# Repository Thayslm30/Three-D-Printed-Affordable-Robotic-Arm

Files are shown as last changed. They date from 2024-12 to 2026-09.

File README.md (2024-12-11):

# T.A.R.A. - Three-D Printed Affordable Robotic Arm

This repository includes the code, 3D printing files, and documentation to build the industrial robot arm named **T.A.R.A.**. This project aims to make robotics accessible by providing a low-cost and customizable solution for education, research, and small-scale industry applications.



---

## What's Included

This repository contains:

1. **3D Printing Files**: STL files for all robot parts.
2. **Electronics and Circuit Diagrams**: Wiring guides.
3. **Software**:
   - Arduino code to control de robot
   - Arduino code for troubleshooting
   - Jupyter Notebobks with the Python code to run simulations of the robot
4. **Documentation**:
   - Bill of materials (BOM) https://docs.google.com/document/d/1PwCRcLvzc4oVpurYSVTbRW2TU2EedRhl2yPV-Ze2hmc/edit?usp=sharing

---

## Getting Started

### Prerequisites

To replicate this project, you’ll need the following:
- **3D Printer**: Compatible with PLA or ABS filament.
- **Electronics**: 
  - Microcontroller (Arduino)
  - Servo motors (MG996R, SG90SR, etc.)
  - Power supply and wires
- **Software**:
  - Python 3.8+ https://www.python.org
  - Arduino IDE (for firmware upload) https://www.arduino.cc/en/software
  - Autodesk Fusion 360 (or any software that allows you to view and modify the 3D printing .stl files) https://www.autodesk.com/products/fusion-360/overview?term=1-YEAR&tab=subscription
  - Jupyter Notebook https://docs.jupyter.org/en/latest/
  - Pinocchio Library https://stack-of-tasks.github.io/pinocchio/
  - Meshcat Library https://pypi.org/project/meshcat/
  - Conda for environment management https://anaconda.org/anaconda/conda

### Steps to Build

1. **Clone the Repository**:
   ```bash
   git clone https://github.com/Thayslm30/Three-D-Printed-Affordable-Robotic-Arm.git
2.  **3D Print the parts**:
     - All the parts can be printed with a 20% infill, except for the base, which has to be 50% to be able to handle the weight of all the robot.
     - All the parts can be printed without supports and without adhesions.
       
3.  **Build the circuit**:
![Figure 11](https://github.com/user-attachments/assets/9e1a0557-dbdc-4448-9370-accc07058d7d)
  
4.  **Assemble the robot**  
   - Starting from top motor at the gripper, the convention is hand servo, wrist servo, elbow servo, shoulder servo, and base servo inside the base.
   - The micro servo goes in the hand joint.
   - The standard servos are for the wrist, elbow, and base joints.
   - The High torque servo is for the shoulder joint.
   - The joints and links have spaces to pass the cables through
   - Use the complete 3D model available in the 3D printing file, to use as a reference of how the parts should fit together. Attach the halves of the links using the screws mentioned in the BOM.
   - The boards can be organized inside the base of the robot.
     
5.  **Running the code**
    - Before running the code for the first time, make sure that all the servos are physically disconnected from the links and are allowed to move freely, for them to be able to move to the zero postion for calibration.

### Demos
https://drive.google.com/drive/u/1/folders/1L06COeyFpNktWuyYnfT8AG40fpObh4bi

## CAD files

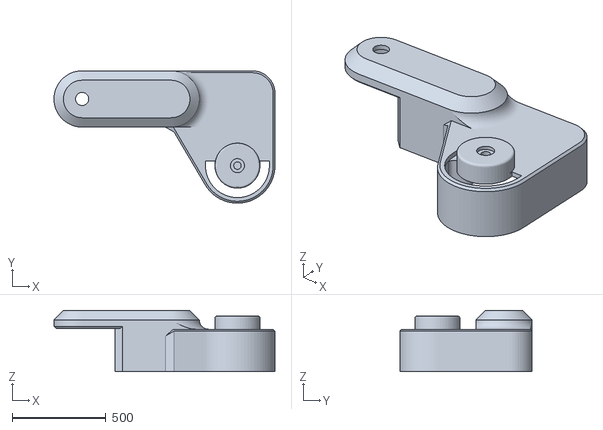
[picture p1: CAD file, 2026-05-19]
3D Printing Files/Link3a.stl
1176.8 x 705.0 x 325.0

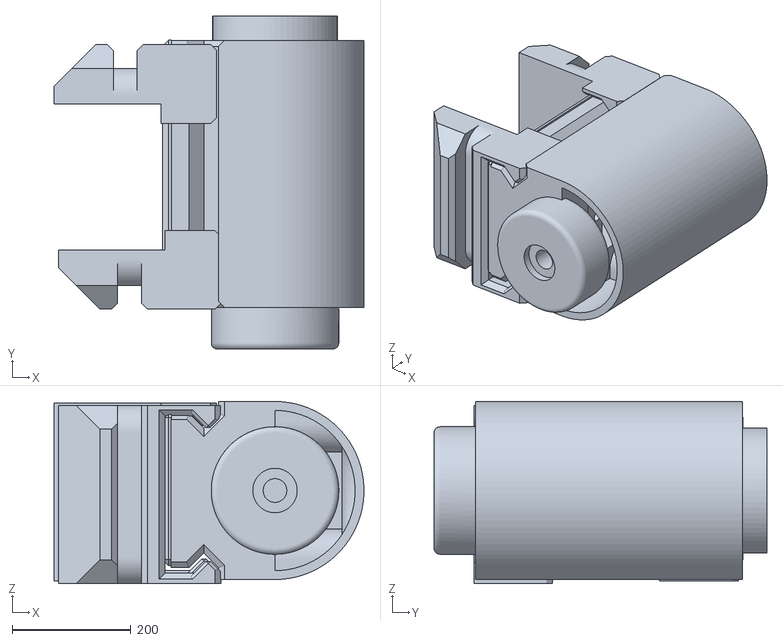
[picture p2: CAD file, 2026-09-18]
Simulation Code/EndEffector_centered.stl
522.1 x 561.0 x 306.7

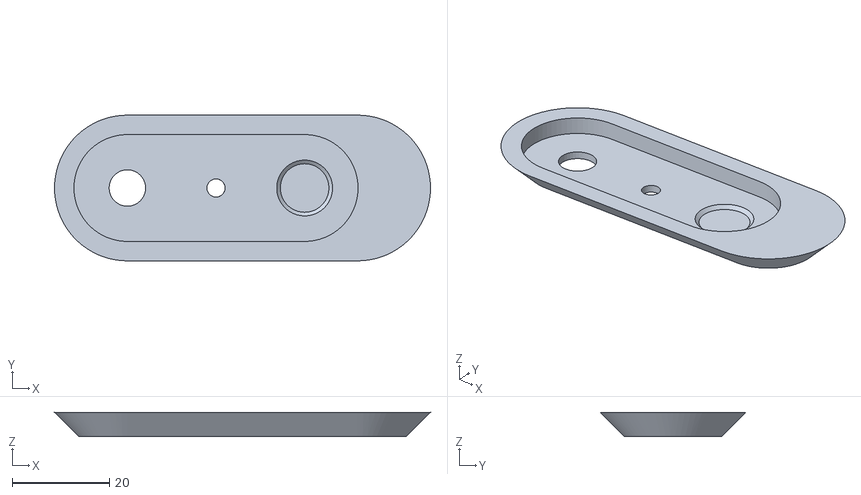
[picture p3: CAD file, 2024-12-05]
3D Printing Files/Link3c.stl
77.4 x 30.0 x 5.00

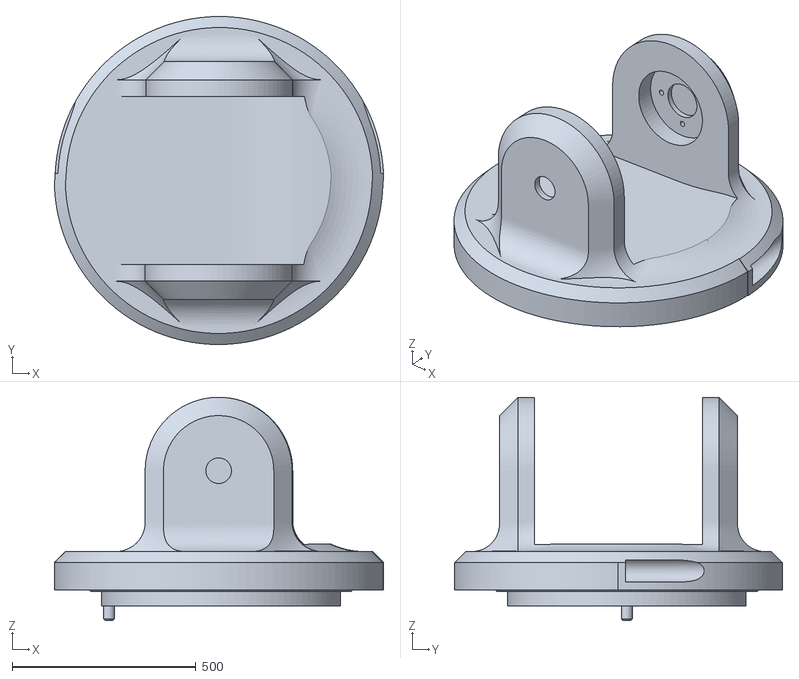
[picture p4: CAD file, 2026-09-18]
Simulation Code/Link1_centered.stl
896.9 x 893.1 x 608.3

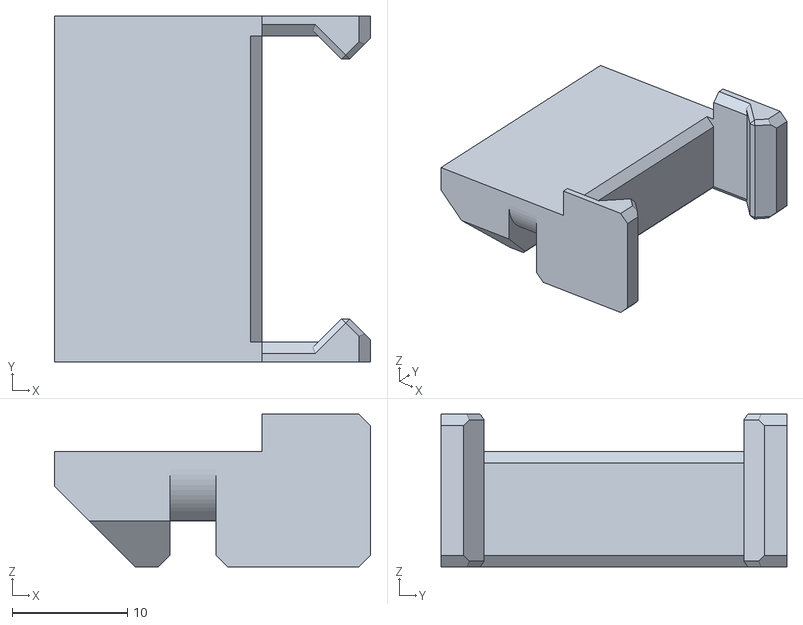
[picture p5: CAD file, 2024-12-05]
3D Printing Files/End_Effector_4.stl
27.4 x 30.0 x 13.2

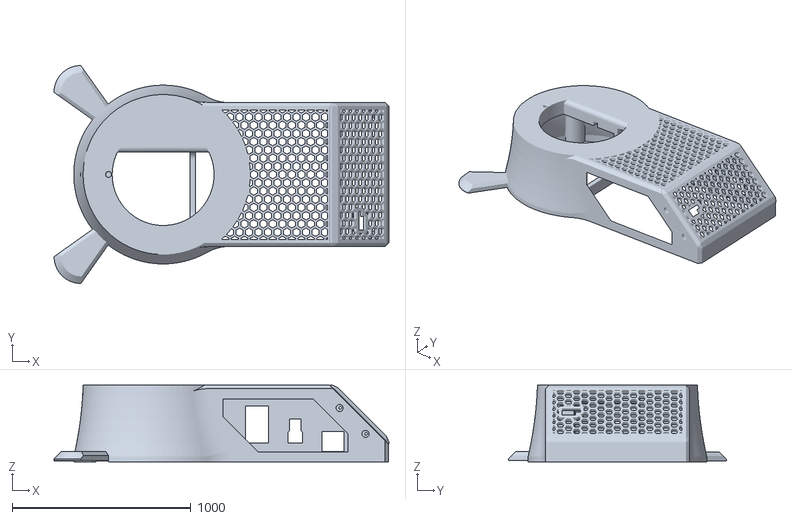
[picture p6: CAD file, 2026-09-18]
Simulation Code/Base_centered.stl
1874.0 x 1219.3 x 430.5

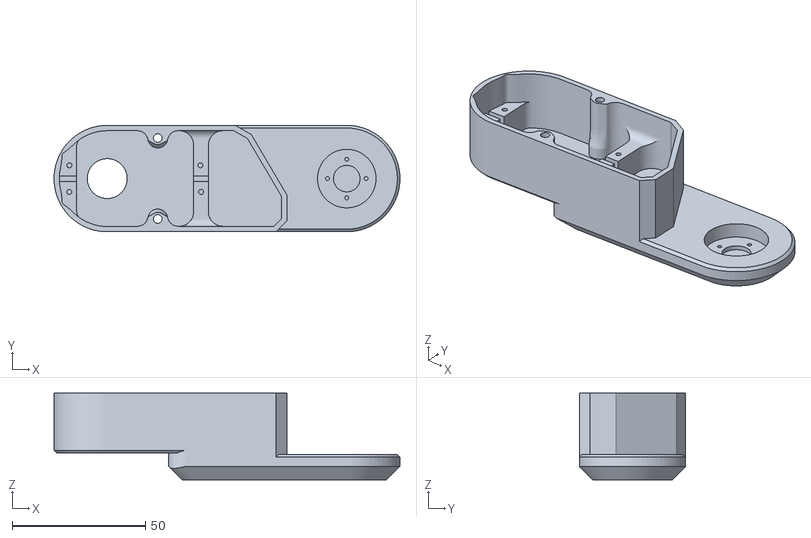
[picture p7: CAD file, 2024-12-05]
3D Printing Files/Link2b.stl
130.0 x 39.9 x 32.5

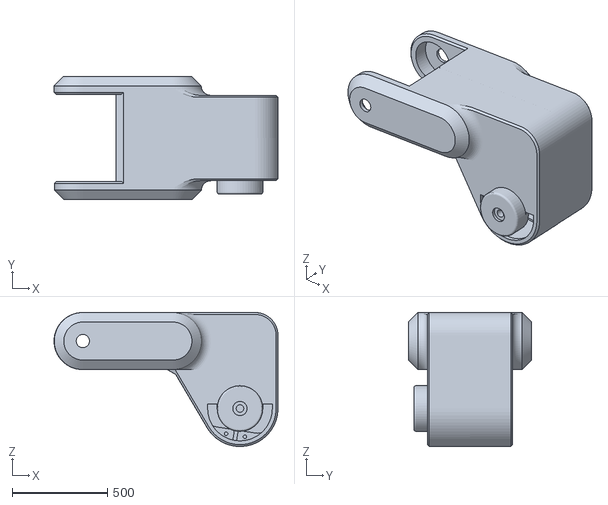
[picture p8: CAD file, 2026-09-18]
Simulation Code/Link3_centered.stl
1178.7 x 649.8 x 705.3

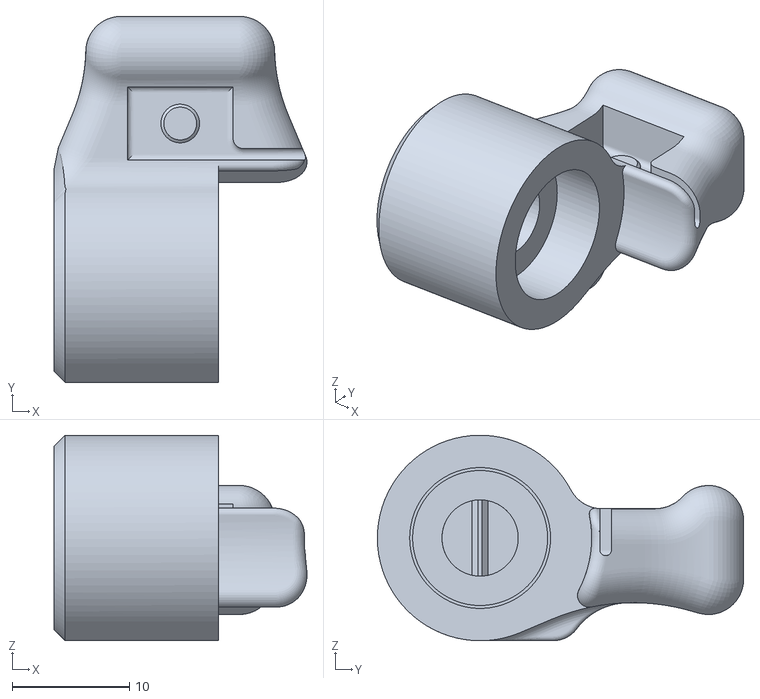
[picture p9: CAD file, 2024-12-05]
3D Printing Files/Mini_End_Effector.stl
21.5 x 31.2 x 17.5

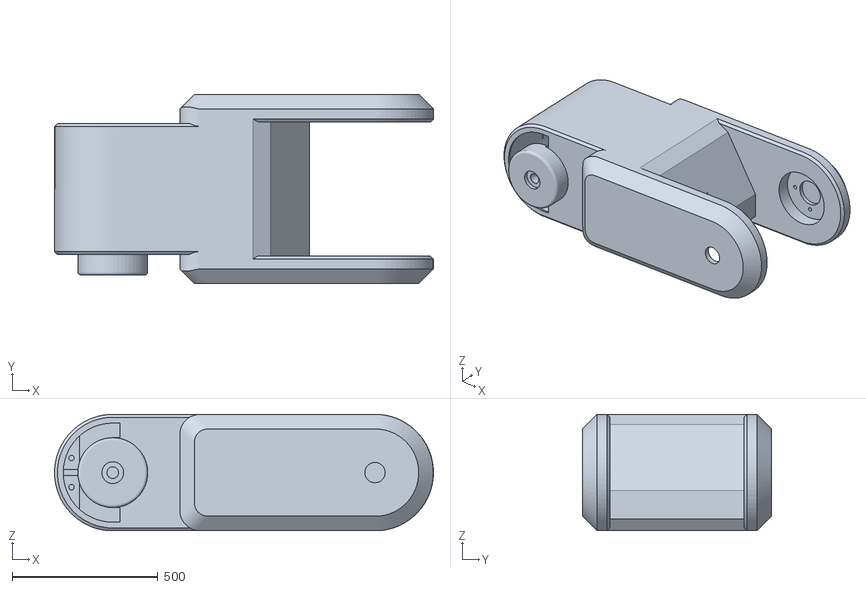
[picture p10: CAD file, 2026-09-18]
Simulation Code/Link2_centered.stl
1300.8 x 649.9 x 399.4

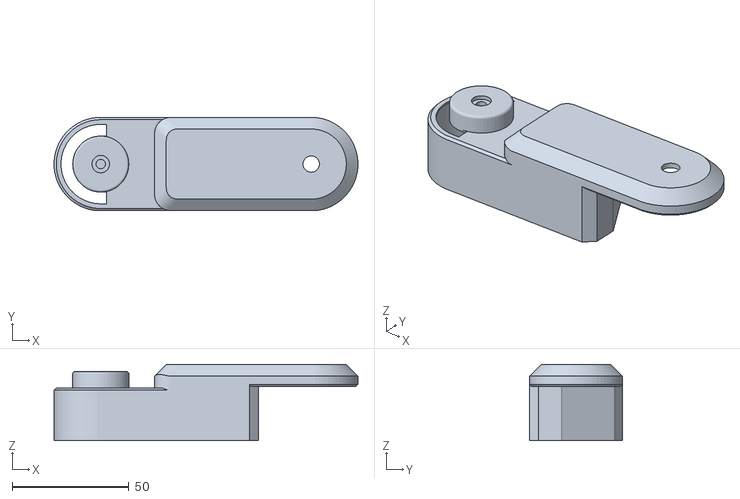
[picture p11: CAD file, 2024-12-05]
3D Printing Files/Link2a.stl
130.0 x 39.9 x 32.5

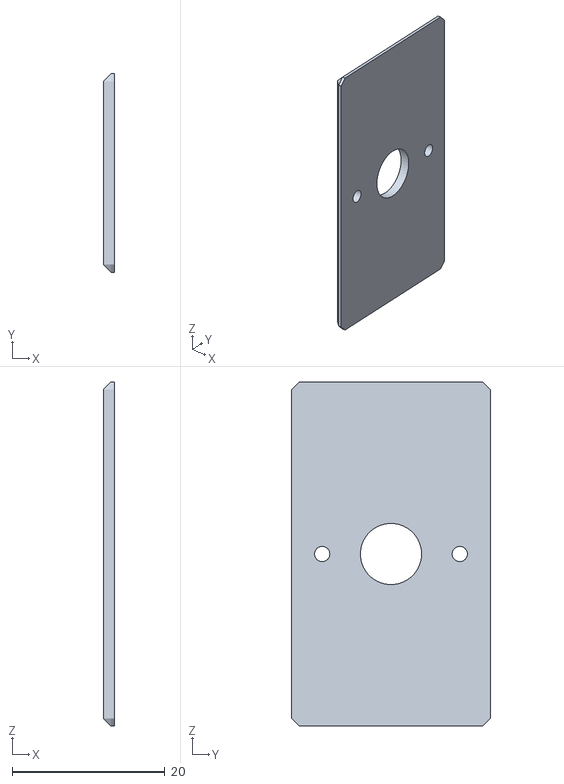
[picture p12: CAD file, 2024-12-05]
3D Printing Files/End_Effector_2.stl
1.50 x 26.0 x 45.0

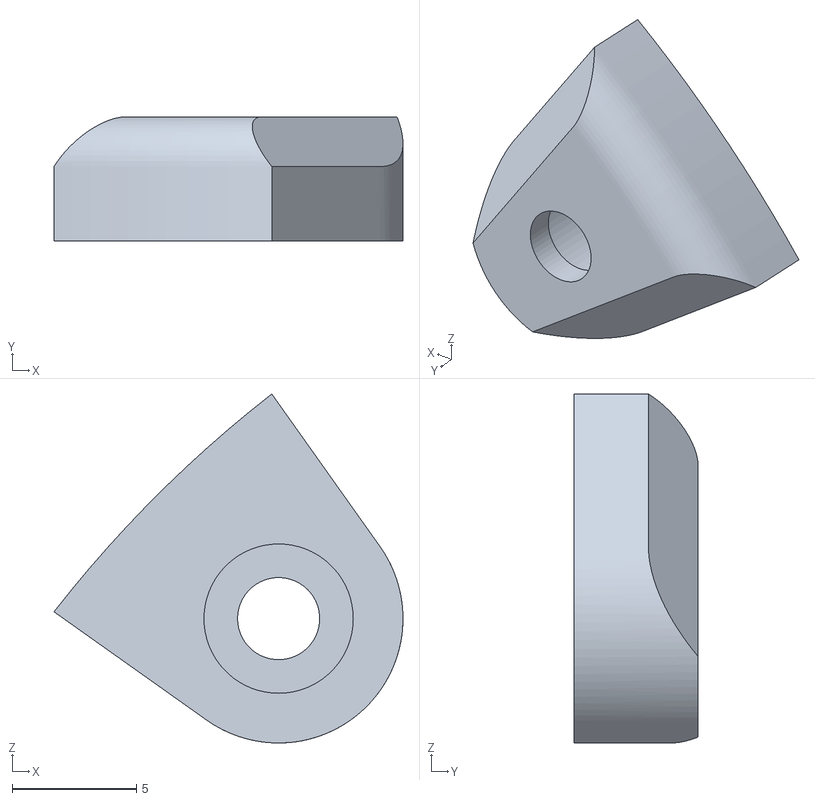
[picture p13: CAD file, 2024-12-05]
3D Printing Files/Support2.stl
14.0 x 5.00 x 14.0

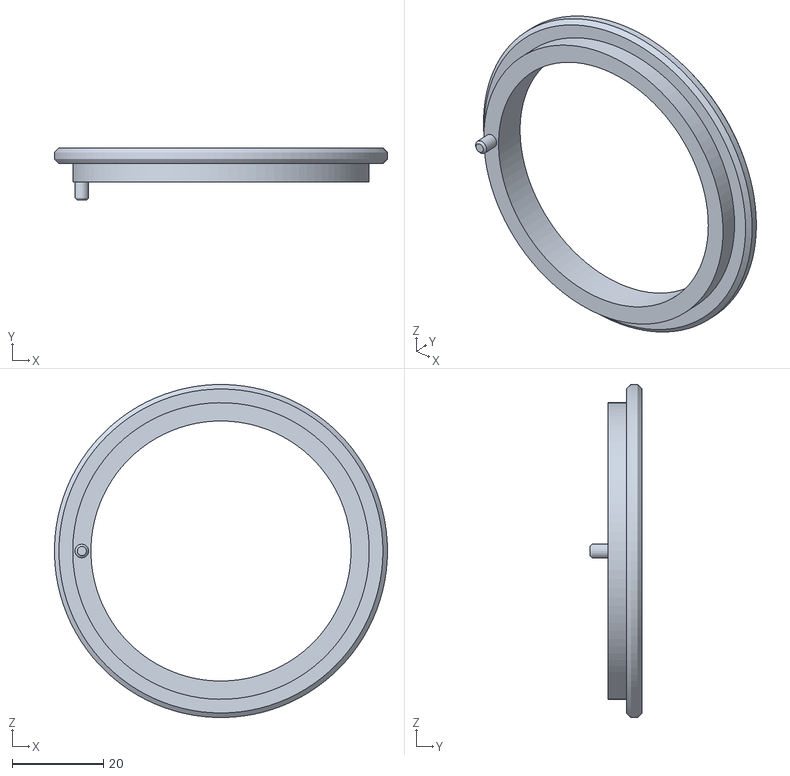
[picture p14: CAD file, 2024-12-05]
3D Printing Files/Base_ring.stl
73.0 x 11.5 x 73.0

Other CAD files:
3D Printing Files/Mini_Link3.stl
3D Printing Files/End_Effector_3.stl
3D Printing Files/Link1a.stl
3D Printing Files/Base.stl
3D Printing Files/End_Effector_1.stl
3D Printing Files/Link1b.stl
3D Printing Files/Link3b.stl
3D Printing Files/Mini_Base.stl
3D Printing Files/Mini_Link1.stl
3D Printing Files/Mini_Link2.stl

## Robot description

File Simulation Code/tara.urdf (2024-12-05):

<robot name="my_robot">
  <!-- Base link -->
  <link name="base_link">
    <visual>
      <origin xyz="0 0 0" rpy="0 0 0"/> <!-- Position the base -->
      <geometry>
        <mesh filename="Base_centered.stl" scale="0.001 0.001 0.001"/>
      </geometry>
    </visual>
  </link>

  <!-- Joint 1: Revolute joint in Z-axis -->
  <joint name="joint_1" type="revolute">
    <parent link="base_link"/>
    <child link="link_0"/>
    <!-- Place the joint where the links connect (relative to base_link) -->
    <origin xyz="0 0 0" rpy="0 0 0"/> <!-- Adjust as necessary -->
    <axis xyz="0 0 1"/> <!-- Rotation along Z-axis -->
    <limit effort="100" velocity="1.0" lower="-3.14" upper="3.14"/>
  </joint>

  <!-- Link 0 -->
  <link name="link_0">
    <visual>
      <!-- The origin should be relative to the joint, not global (relative to base_link) -->
      <origin xyz="0 0 0" rpy="0 0 0"/> <!-- Ensure this is correct -->
      <geometry>
        <mesh filename="Link1_centered.stl" scale="0.001 0.001 0.001"/>
      </geometry>
    </visual>
  </link>
  <!-- Joint 2: Revolute joint in y-axis -->
  <joint name="joint_2" type="revolute">
    <parent link="link_0"/>
    <child link="link_1"/>
    <!-- Place the joint where the links connect (relative to base_link) -->
    <origin xyz="0 0 0.73" rpy="0 0 0"/> <!-- Adjust as necessary -->
    <axis xyz="0 1 0"/> <!-- Rotation along Y-axis -->
    <limit effort="100" velocity="1.0" lower="0" upper="-3.14"/>
  </joint>

  <!-- Link 1 -->
  <link name="link_1">
    <visual>
      <!-- The origin should be relative to the joint, not global (relative to base_link) -->
      <origin xyz="0 0 0" rpy="0 0 0"/> <!-- Ensure this is correct -->
      <geometry>
        <mesh filename="Link2_centered.stl" scale="0.001 0.001 0.001"/>
      </geometry>
    </visual>
  </link>
  <!-- Joint 3: Revolute joint in y-axis -->
  <joint name="joint_3" type="revolute">
    <parent link="link_1"/>
    <child link="link_2"/>7
    <!-- Joint where the links connect (relative to base_link) -->
    <origin xyz="0.90 0 0" rpy="0 0 0"/> <!-- Adjust as necessary -->
    <axis xyz="0 1 0"/> <!-- Rotation along Y-axis -->
    <limit effort="100" velocity="1.0" lower="0" upper="1.57"/>
  </joint>

  <!-- Link 2 -->
  <link name="link_2">
    <visual>
      <!-- The origin should be relative to the joint, not global (relative to base_link) -->
      <origin xyz="0 0 0" rpy="0 0 0"/> <!-- Ensure this is correct -->
      <geometry>
        <mesh filename="Link3_centered.stl" scale="0.001 0.001 0.001"/>
      </geometry>
    </visual>
  </link>
  <!-- Joint 4: Revolute joint in y-axis -->
  <joint name="joint_4" type="revolute">
    <parent link="link_2"/>
    <child link="end_effector"/>
    <!-- Joint where the links connect (relative to base_link) -->
    <origin xyz="-0.83 0 0.35" rpy="0 0 0"/> <!-- Adjust as necessary -->
    <axis xyz="0 1 0"/> <!-- Rotation along Y-axis -->
    <limit effort="100" velocity="1.0" lower="-1.57" upper="1.57"/>
  </joint>

  <!-- End-Effector -->
  <link name="end_effector">
    <visual>
      <!-- The origin should be relative to the joint, not global (relative to base_link) -->
      <origin xyz="0 0 0" rpy="0 0 0"/> <!-- Ensure this is correct -->
      <geometry>
        <mesh filename="EndEffector_centered.stl" scale="0.001 0.001 0.001"/>
      </geometry>
    </visual>
  </link>
</robot>

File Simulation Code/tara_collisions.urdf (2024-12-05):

<robot name="my_robot">
  <!-- Base link -->
  <link name="base_link">
    <visual>
      <origin xyz="0 0 0" rpy="0 0 0"/> <!-- Position the base -->
      <geometry>
        <mesh filename="Base_centered.stl" scale="0.001 0.001 0.001"/>
      </geometry>
    </visual>
    <collision>
      <origin xyz="0.4 0 0.2" rpy="0 0 0"/> 
      <geometry>
        <box size="1.8 1.0 0.3"/>  <!-- Adjust size to fit the base -->
      </geometry>
    </collision>
  </link>

  <!-- Joint 1: Revolute joint in Z-axis -->
  <joint name="joint_1" type="revolute">
    <parent link="base_link"/>
    <child link="link_0"/>
    <origin xyz="0 0 0" rpy="0 0 0"/> <!-- Adjust as necessary -->
    <axis xyz="0 0 1"/> <!-- Rotation along Z-axis -->
    <limit effort="100" velocity="1.0" lower="-3.14" upper="3.14"/>
  </joint>

  <!-- Link 0 -->
  <link name="link_0">
    <visual>
      <origin xyz="0 0 0" rpy="0 0 0"/> <!-- Ensure this is correct -->
      <geometry>
        <mesh filename="Link1_centered.stl" scale="0.001 0.001 0.001"/>
      </geometry>
    </visual>
    <collision>
      <origin xyz="0 0 0" rpy="0 0 0"/>
      <geometry>
        <box size="0 0 0"/>  <!-- Adjust size to fit Link 0 -->
      </geometry>
    </collision>
  </link>

  <!-- Joint 2: Revolute joint in Y-axis -->
  <joint name="joint_2" type="revolute">
    <parent link="link_0"/>
    <child link="link_1"/>
    <origin xyz="0 0 0.73" rpy="0 0 0"/> <!-- Adjust as necessary -->
    <axis xyz="0 1 0"/> <!-- Rotation along Y-axis -->
    <limit effort="100" velocity="1.0" lower="-3.14" upper="0"/> <!-- Reversed limits -->
  </joint>

  <!-- Link 1 -->
  <link name="link_1">
    <visual>
      <origin xyz="0 0 0" rpy="0 0 0"/> <!-- Ensure this is correct -->
      <geometry>
        <mesh filename="Link2_centered.stl" scale="0.001 0.001 0.001"/>
      </geometry>
    </visual>
    <collision>
      <origin xyz="0.5 0 0" rpy="0 0 0"/>
      <geometry>
        <box size="0.8 0.6 0.4"/>  <!-- Adjust size to fit Link 1 -->
      </geometry>
    </collision>
  </link>

  <!-- Joint 3: Revolute joint in Y-axis -->
  <joint name="joint_3" type="revolute">
    <parent link="link_1"/>
    <child link="link_2"/>
    <origin xyz="0.90 0 0" rpy="0 0 0"/> <!-- Adjust as necessary -->
    <axis xyz="0 1 0"/> <!-- Rotation along Y-axis -->
    <limit effort="100" velocity="1.0" lower="0" upper="1.57"/>
  </joint>

  <!-- Link 2 -->
  <link name="link_2">
    <visual>
      <origin xyz="0 0 0" rpy="0 0 0"/> <!-- Ensure this is correct -->
      <geometry>
        <mesh filename="Link3_centered.stl" scale="0.001 0.001 0.001"/>
      </geometry>
    </visual>
    <collision>
      <origin xyz="-0.3 0 0.4" rpy="0 0 0"/>
      <geometry>
        <box size="1 0.5 0.25"/>  <!-- Adjust size to fit Link 2 -->
      </geometry>
    </collision>
  </link>

  <!-- Joint 4: Revolute joint in Y-axis -->
  <joint name="joint_4" type="revolute">
    <parent link="link_2"/>
    <child link="end_effector"/>
    <origin xyz="-0.83 0 0.35" rpy="0 0 0"/> <!-- Adjust as necessary -->
    <axis xyz="0 1 0"/> <!-- Rotation along Y-axis -->
    <limit effort="100" velocity="1.0" lower="-1.57" upper="1.57"/>
  </joint>

  <!-- End-Effector -->
  <link name="end_effector">
    <visual>
      <origin xyz="0 0 0" rpy="0 0 0"/> <!-- Ensure this is correct -->
      <geometry>
        <mesh filename="EndEffector_centered.stl" scale="0.001 0.001 0.001"/>
      </geometry>
    </visual>
    <collision>
      <origin xyz="-0.3 0 0" rpy="0 0 0"/>
      <geometry>
        <box size="0.2 0.5 0.3"/>  <!-- Adjust size to fit Link 2 -->
      </geometry>
    </collision>
  </link>
</robot>

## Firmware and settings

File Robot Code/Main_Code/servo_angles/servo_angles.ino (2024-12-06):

#include <Wire.h>
#include <Adafruit_PWMServoDriver.h>

Adafruit_PWMServoDriver pwm = Adafruit_PWMServoDriver();

#define FREQUENCY 50 // Servo frequency in Hz (standard 50 Hz)

// Servo-specific pulse width ranges
#define MG996R_MIN  1000   // MG996R: Minimum pulse width in microseconds
#define MG996R_MAX  2000   // MG996R: Maximum pulse width in microseconds
#define SG90_MIN    500    // SG90: Minimum pulse width in microseconds
#define SG90_MAX    2400   // SG90: Maximum pulse width in microseconds
#define HIGH_TORQUE_MIN 500  // 20KG Servo: Minimum pulse width in microseconds
#define HIGH_TORQUE_MAX 2500 // 20KG Servo: Maximum pulse width in microseconds

// Function to convert angle to pulse width for specific servo
int angleToPulse(int angle, int minPulse, int maxPulse) {
  return map(angle, 0, 180, minPulse, maxPulse); // Adjusted for servo-specific range
}

// Function to move a servo to a specified angle
void moveServo(int channel, int angle, int minPulse, int maxPulse) {
  int pulse = angleToPulse(angle, minPulse, maxPulse); // Get the pulse width for the angle
  int pwmValue = pulse * FREQUENCY * 4096L / 1000000L; // Convert to Adafruit scale
  pwm.setPWM(channel, 0, pwmValue); // Send the signal to the specified channel

  // Debug output
  Serial.print("Channel ");
  Serial.print(channel);
  Serial.print(": Angle = ");
  Serial.print(angle);
  Serial.print(", Pulse Width (us) = ");
  Serial.println(pulse);
}

void setup() {
  Serial.begin(9600);
  Serial.println("Testing servo positions...");

  pwm.begin();               // Initialize the Adafruit board
  pwm.setPWMFreq(FREQUENCY); // Set PWM frequency to 50 Hz

  // Define servo channels and angles
  int channels[5] = {11, 12, 13, 14, 15}; // Channels for the 5 servos
  //int angles[5] = {45, 90, -100, 200, 100};        // Set all servos to 0 degrees for testing
  int angles[5] = {0, 0, -0, 0, 0}; 
  // Move each servo to its specified angle
  for (int i = 0; i < 5; i++) {
    if (channels[i] == 11) { // SG90
      moveServo(channels[i], angles[i], SG90_MIN, SG90_MAX);
    } else if (channels[i] == 15) { // High Torque Servo
      moveServo(channels[i], angles[i], HIGH_TORQUE_MIN, HIGH_TORQUE_MAX);
    } else { // MG996R (default for other channels)
      moveServo(channels[i], angles[i], MG996R_MIN, MG996R_MAX);
    }
    delay(1000); // Add delay between movements
  }
}

void loop() {
  // Nothing to do here
}

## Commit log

2024-12-05 Add files via upload
    STL Files for 3d printing
    [Base.stl, Base_ring.stl, End_Effector_1.stl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]
2024-12-05 Add files via upload
    Forward Kinematics code
2024-12-05 Add files via upload
    rest of kinematics code and urdf files for simulation
    [tara.urdf, tara_collisions.urdf]
2024-12-05 Add files via upload
    trouble shooting code for servos and servo driver
